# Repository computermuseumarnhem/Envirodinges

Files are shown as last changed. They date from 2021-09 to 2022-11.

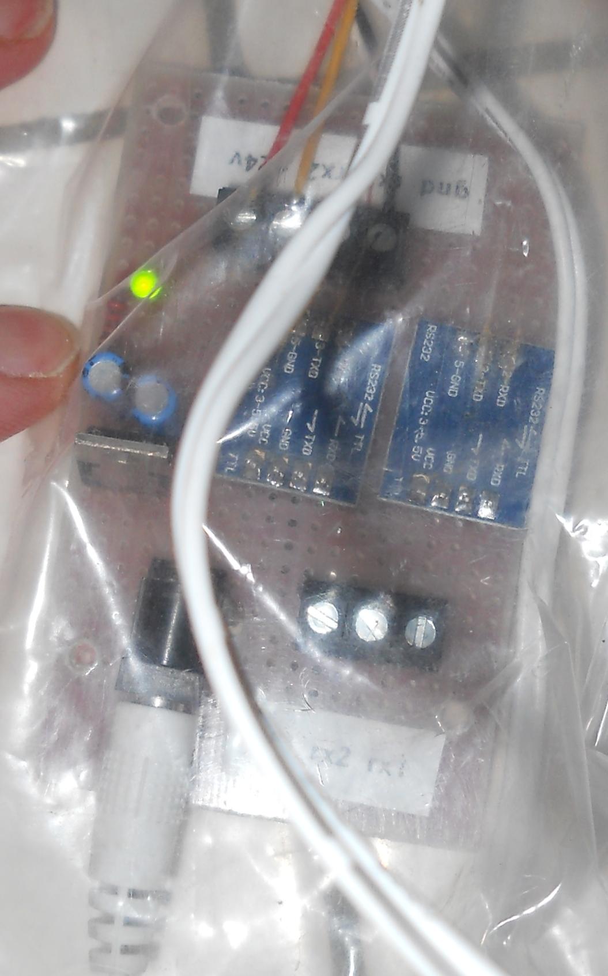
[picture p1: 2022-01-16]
dscn2125_crop.jpg

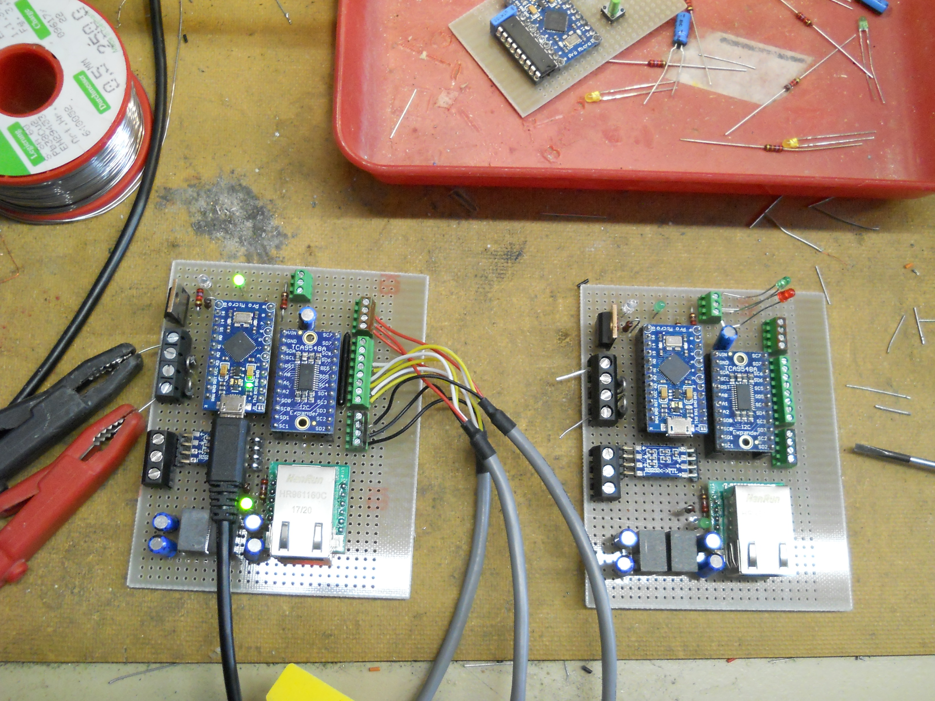
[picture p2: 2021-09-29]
dscn2068.jpg

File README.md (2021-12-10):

# Envirodinges
Veredelde fan controller voor het ventileren van de opslagcontainers. 

Fan aan/uit wordt gestuurd door een Arduino Pro Micro op basis van AM2315 thermo/hygro sensors (1 buiten, 2 binnen) zodat er geventileerd wordt als de luchttemperatuur >10C boven de dauwpunttemperatuur ligt waardoor er binnen geen kans is op condens van de aangezogen lucht.

Status output 1x/minuut via RS232, zie Envirodinges.log.

LAN hardware met W5500 TCP/IP chip aanwezig, maar niet gebruikt door gebrek aan programmaruimte.

Omdat de AM2315 geen instelbaar I2C adres heeft worden ze via een multiplexer (TCA9548) aangesloten.

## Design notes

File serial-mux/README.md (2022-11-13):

# Serial Multiplexer.

## Envirodinges

De twee Envirodingesen sturen regels over twee RS232-lijnen naar iets wat ze zou kunnen loggen.

## Multiplexer

Een Pro Micro met een hardware serial en een software serial leest
deze RS232 lijnen en (omdat de containers zelf de prefix met 'container1' of 'container2' doet) buffert
ze per regel en stuurt ze door via de USB-serial.

De Pro Micro is gemonteerd op een board met schroefaansluitingen, die is eigenlijk bedoeld voor de Arduino Nano, maar
de Pro Micro past ook.

### Seriele poorten

Omdat de SoftwareSerial op de Pro Micro (ATmega32U4) alleen werkt op poorten waar een pin change interrupt actief kan zijn, worden pin 8 en 9 voor respectievelijk RX en TX gebruikt. De vorige versies op respectievelijk pin 4 en 5, daarna 2 en 3 bleken niet te werken totdat ik de handleiding beter had gelezen.

## Wat te doen met de data

Een IOTStack-gebaseerde Pi (Mosquitto, NodeRed, InfluxDB, Grafana) is ingericht om alles te kunnen netwerken.

- NodeRed luistert naar de USB-serial, vertaalt de puntjes naar slashes en publiceert de key/value pairs als topic/payload naar de Mosquitto MQTT broker.
- NoderRed stuurt de key/value pairs ook naar InfluxDB
- Grafana leest InfluxDB en maakt er shiny plaatjes van.

Bovenstaande kan natuurlijk allemaal gescrapt worden als gebruik kan worden gemaakt van een al bestaande machine die USB-serial kan lezen, en de gegevens naar een reeds bestaande MQTT te sturen. Et Cetera.

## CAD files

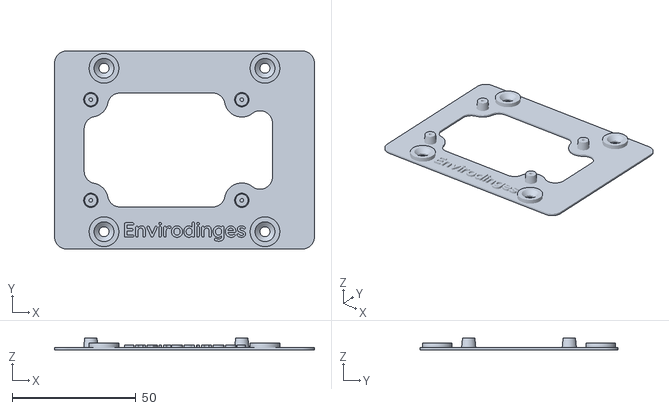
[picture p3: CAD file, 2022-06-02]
serial-mux/bevestiging/serial-module.stl
105.0 x 80.0 x 5.00

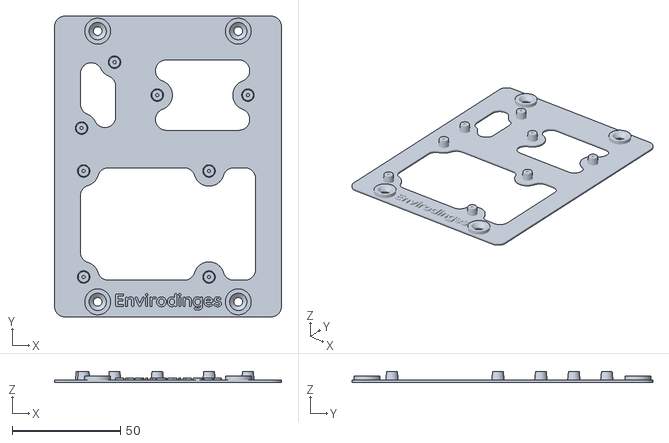
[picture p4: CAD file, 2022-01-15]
serial-mux/bevestiging/bevestiging.stl
105.0 x 139.2 x 5.00

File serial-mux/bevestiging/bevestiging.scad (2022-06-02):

$fn = 90;

want="serial";

function inch(n) = 25.4 * n;

PI_BOARD = [85, 56, 1.25];
PWR_BOARD = [inch(0.80), inch(1.70), inch(0.04)];
NANO_BOARD = [53, 36.5, inch(0.05)];
SERIAL_BOARD = [80, 50, 1.6];

PI_HOLE_LOCATIONS =	[[3.5, 3.5], [61.5, 3.5], [3.5, 52.5], [61.5, 52.5]];
PWR_HOLE_LOCATIONS = [[inch(0.10), inch(0.25)], [inch(0.70), inch(1.45)]];
NANO_HOLE_LOCATIONS = [[26.5-inch(1.65/2), 36.5/2], [26.5+inch(1.65/2), 36.5/2]];

SERIAL_MARGIN = SERIAL_BOARD.y/2 - inch(1.6/2);

SERIAL_HOLE_LOCATIONS = [
    [SERIAL_MARGIN, SERIAL_MARGIN],
    [SERIAL_MARGIN + inch(2.4), SERIAL_MARGIN],
    [SERIAL_MARGIN, SERIAL_MARGIN + inch(1.6)],
    [SERIAL_MARGIN + inch(2.4), SERIAL_MARGIN + inch(1.6)]
];

echo(SERIAL_HOLE_LOCATIONS);
module chamfer(radius) {
    offset(r=radius) offset(r=-radius) children();
}

module plaat(size, radius, flat=false) {
    if (flat) {
        chamfer(radius) square([size.x, size.y]);
    } else {
        linear_extrude(size.z) plaat(size, radius, true);
    }
}

module center(dim) {
    //translate(-[dim.x, dim.y, 0]/2) 
        children();
}

module pi_board(h = 0, flat=false) {
    translate([0, 0, h]) center(PI_BOARD) plaat(PI_BOARD, 3.5, flat);
}
module pwr_board(h = 0, flat=false) {
    translate([0, 0, h]) center(PWR_BOARD) plaat(PWR_BOARD, 0, flat);
}
module nano_board(h = 0, flat=false) {
    translate([0, 0, h]) center(NANO_BOARD) plaat(NANO_BOARD, 0, flat);
}

module serial_board(h = 0, flat=false) {
    translate([0, 0, h]) center(SERIAL_BOARD) plaat(SERIAL_BOARD, 0, flat);
}

module pi_hole_locations() {
    center(PI_BOARD) {
        for (hole = PI_HOLE_LOCATIONS) {
            translate(hole) children();
        }
    }
}
module pwr_hole_locations() {
    center(PWR_BOARD) {
        for (hole = PWR_HOLE_LOCATIONS) {
            translate(hole) children();
        }
    }
}
module nano_hole_locations() {
    center(NANO_BOARD) {
        for (hole = NANO_HOLE_LOCATIONS) {
            translate(hole) children();
        }
    }
}

module serial_hole_locations() {
    center(SERIAL_BOARD) {
        for (hole = SERIAL_HOLE_LOCATIONS) {
            translate(hole) children();
        }
    }
}  

module post() {
    difference() {
        cylinder(d1=6, d2=5, h=5);
        cylinder(d=1.5, h=5);
    }
}

module mount(diff=false) {
    if (!diff) {
        cylinder(d=12, h=3);
    } else {
        cylinder(d=4, h=3);
        translate([0,0,1]) cylinder(d1=4, d2=8, h=2);
    }
}

module mqtt_holes(mounts) {
    
    linear_extrude(2)
    chamfer(5) offset(r=-2)
    difference() {
        union() {
            translate([ pi_top, pi_left, 0]) {
                pi_board(flat=true);
            }
            translate([ pwr_top,  pwr_left, 0]) {
                pwr_board(flat=true);
            }
            translate([ nano_top,  nano_left, 0]) {
                nano_board(flat=true);
            }
        };
        for (m = mounts) {
            translate(m) circle(d=14);
        }
        translate([ pi_top, pi_left, 0]) {
            pi_hole_locations() circle(d=10);
        }
        translate([ pwr_top,  pwr_left, 0]) {
            pwr_hole_locations() circle(d=10);
        }
        translate([ nano_top,  nano_left, 0]) {
            nano_hole_locations() circle(d=10);
        }
    }
}


module serial_holes(mounts) {
    
    linear_extrude(2)
    chamfer(5) offset(r=-2)
    difference() {
        union() {
            translate([ serial_top, serial_left, 0]) {
                serial_board(flat=true);
            }
        };
        for (m = mounts) {
            translate(m) circle(d=14);
        }
        translate([ serial_top, serial_left, 0]) {
            serial_hole_locations() circle(d=10);
        }
    }
}


module name(t) {
    linear_extrude(2)
        text(t, font="Quicksand:style=Bold", size=6, halign="center", valign="center");
}

pi_left = 0;
pwr_left = pi_left + PI_BOARD.y + 10;
nano_left = pwr_left + PWR_BOARD.y/2 - (NANO_BOARD.y/2);

serial_left = 0;

pi_top = 0;
pwr_top = 0;
nano_top = pi_top + PI_BOARD.x - NANO_BOARD.x;

serial_top = 0;

module mqtt_module() {

    base_left = -15;
    base_top = -10;
    base_width = 15 + PI_BOARD.y + 10 + PWR_BOARD.y + 15;
    base_height = 10 + PI_BOARD.x + 10;


    translate([ pi_top, pi_left, 0]) {
        % pi_board(5);
        pi_hole_locations() post();
    }
    translate([ pwr_top,  pwr_left, 0]) {
        % pwr_board(5);
        pwr_hole_locations() post();
    }
    translate([ nano_top,  nano_left, 0]) {
        % nano_board(5);
        nano_hole_locations() post();
    }

    from_top = 20;
    from_left = 7;
    mounts = [
        [ base_top + from_top,                base_left + from_left              ],
        [ base_top + from_top,                base_left + base_width - from_left ],
        [ base_top + base_height - from_top,  base_left + from_left              ],
        [ base_top + base_height - from_top,  base_left + base_width - from_left ]
    ];

    difference() {
        union() {
            translate([base_top, base_left, 0]) {
                plaat([base_height, base_width, 1], 5);
            }
            for (m = mounts) {
                translate(m) mount();
            }
        };
        for (m = mounts) {
            translate(m) mount(true);
        }
        mqtt_holes(mounts);
    }

    text_center = [(mounts[0].x + mounts[2].x)/2, mounts[0].y];

    translate(text_center) name("Envirodinges");

}
module serial_module() {

    base_left = -15;
    base_top = -10;
    base_width = 15 + SERIAL_BOARD.y + 15;
    base_height = 10 + PI_BOARD.x + 10;


    translate([ serial_top, serial_left, 0]) {
        % serial_board(5);
        serial_hole_locations() post();
    }
    
    from_top = 20;
    from_left = 7;
    mounts = [
        [ base_top + from_top,                base_left + from_left              ],
        [ base_top + from_top,                base_left + base_width - from_left ],
        [ base_top + base_height - from_top,  base_left + from_left              ],
        [ base_top + base_height - from_top,  base_left + base_width - from_left ]
    ];

    difference() {
        union() {
            translate([base_top, base_left, 0]) {
                plaat([base_height, base_width, 1], 5);
            }
            for (m = mounts) {
                translate(m) mount();
            }
        };
        for (m = mounts) {
            translate(m) mount(true);
        }
        serial_holes(mounts);
    }

    text_center = [(mounts[0].x + mounts[2].x)/2, mounts[0].y];

    translate(text_center) name("Envirodinges");

}


if (want=="mqtt") {
    mqtt_module();
}
if (want=="serial") {
    serial_module();
}

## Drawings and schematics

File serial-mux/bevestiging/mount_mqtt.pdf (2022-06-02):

# /home/denz/Drive/CMA/Envirodinges/serial-mux/bevestiging/bevestiging.scad

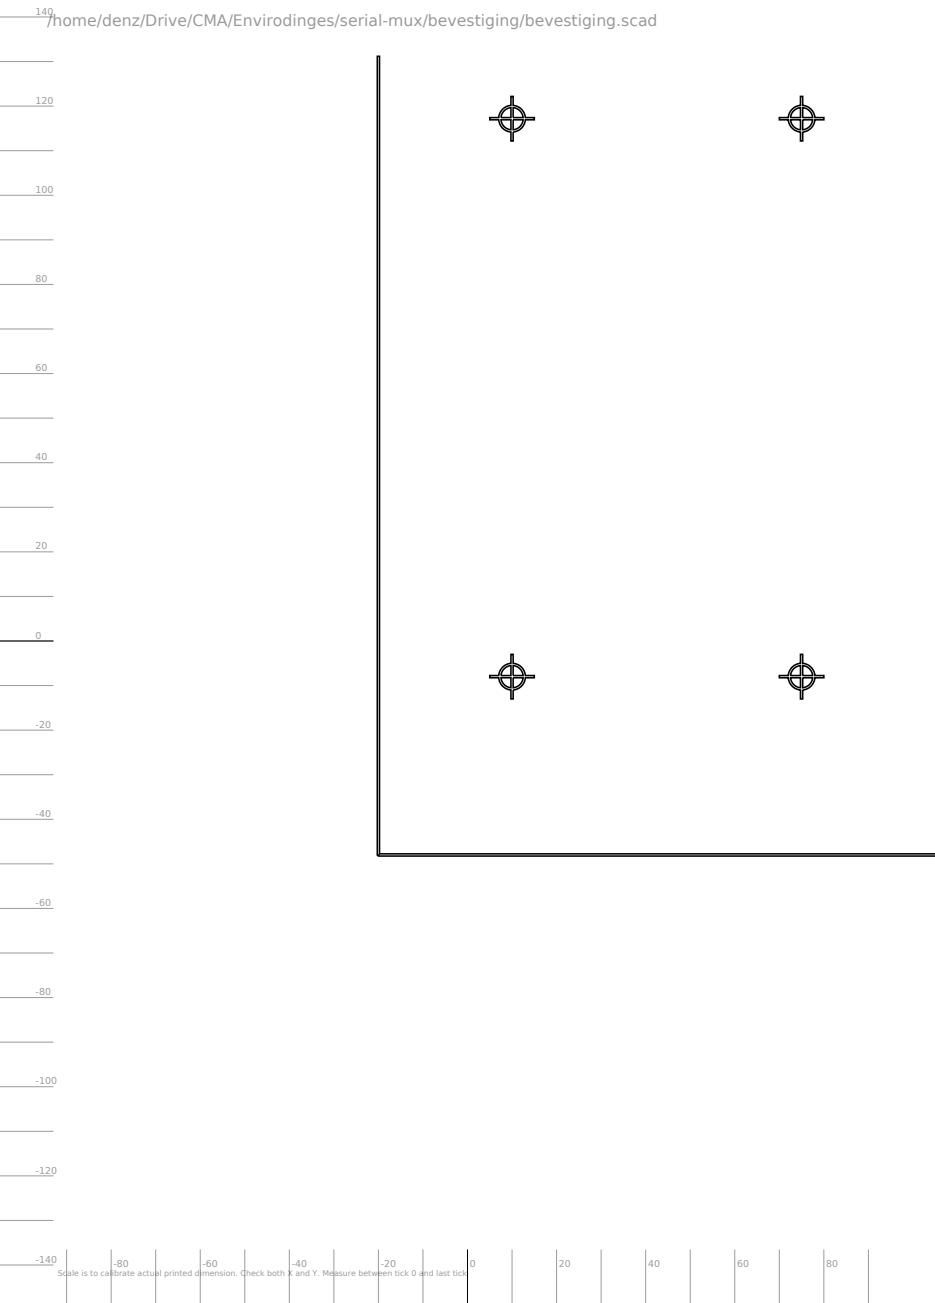
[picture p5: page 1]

Scale is to calibrate actual printed dimension. Check both X and Y. Measure between tick 0 and last tick

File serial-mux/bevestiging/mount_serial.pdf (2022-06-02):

# /home/denz/Drive/CMA/Envirodinges/serial-mux/bevestiging/bevestiging.scad

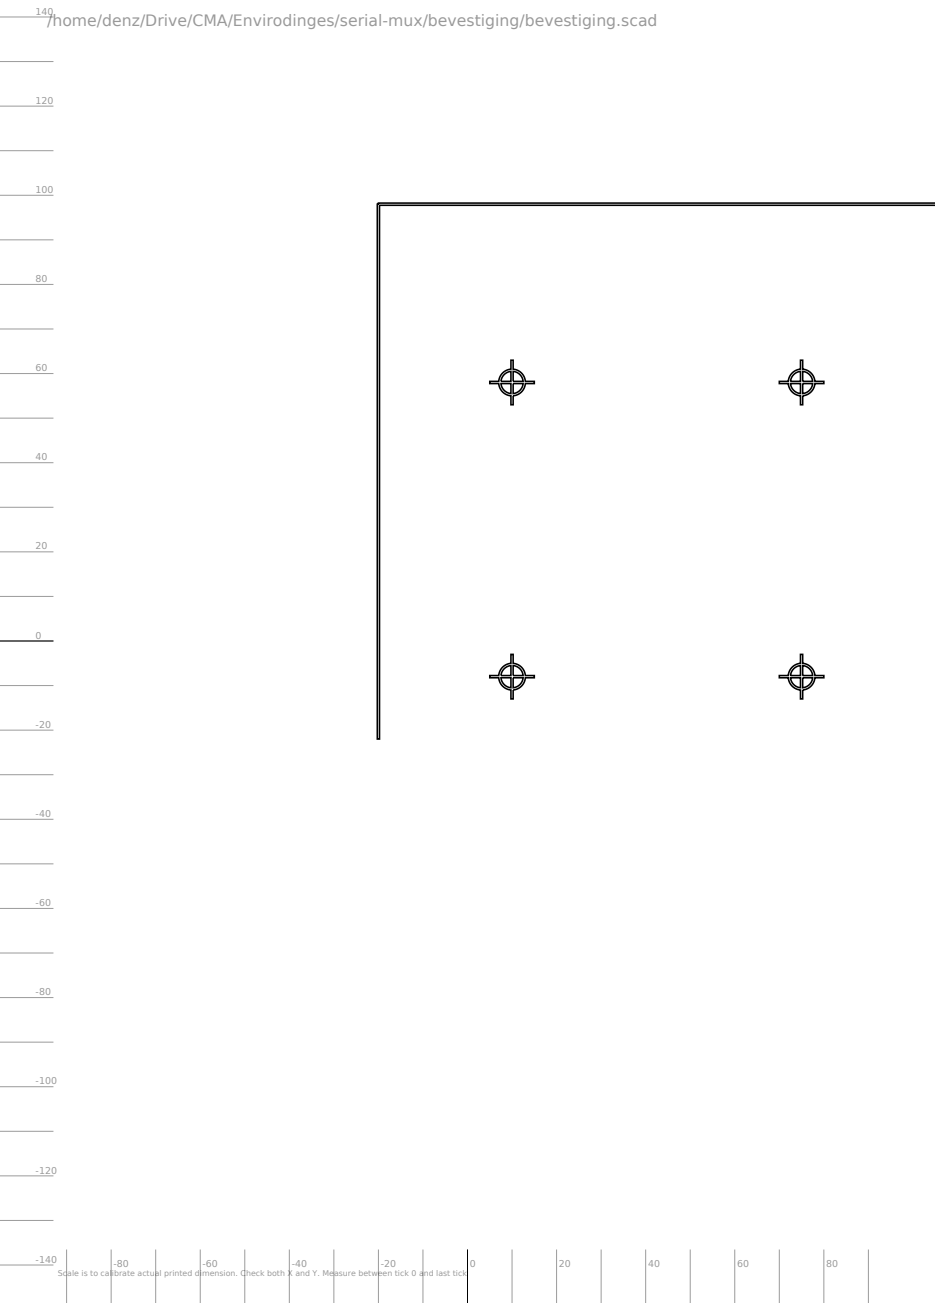
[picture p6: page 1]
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

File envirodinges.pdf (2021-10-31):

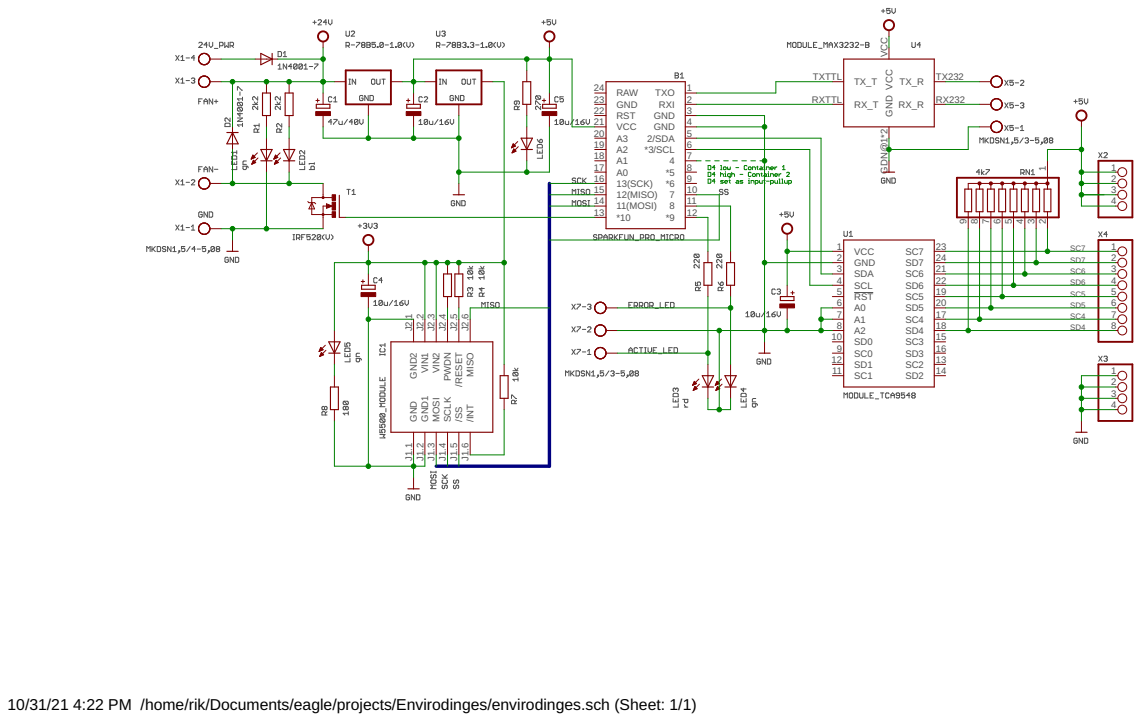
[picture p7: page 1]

7 8 9 10

10/31/21 4:22 PM /home/rik/Documents/eagle/projects/Envirodinges/envirodinges.sch (Sheet: 1/1)

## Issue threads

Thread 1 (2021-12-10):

Parsing of the serial port output

vandenzel, 2021-12-10:
I'm trying to implement a way to read the output of the Envirodingeses with a machine. So I propose the following changes:

Replace all output lines with a key-value pair like this:

    envirodinges.c1.version 0.9
    envirodinges.c1.s1.status ok
    envirodinges.c1.started
    envirodinges.c1.s1.temp 5.3 C
    envirodinges.c1.s1.hum 94.4 %
    envirodinges.c2.s1.status notfound
    envirodinges.c2.s1.status missing

This way a can just split the values and use value[0] as mqtt (and influxdb) topic, and value[1] as the payload.

--
Alex.

Stoneshop, 2021-12-11:
Will look into this.

vandenzel, 2021-12-13:
Ik zat een beetje hieraan te denken:

De tag is een MQTT topic, en bestaat uit

 * ```envirodinges```
 * de naam van de container (van de envirodinges module)
 * de naam van de sensor (indien van toepassing), bijvoorbeeld ```container1```
 * de grootheid (```temperatuur```, ```status```, etc...)

De waarde is dan in het relevante datatype van de grootheid, en bevat geen spaties. Als er na de waarde een spatie en nog meer tekst staat is dat voor de human-readability en wordt door de machine genegeerd.

Bijvoorbeeld:

    envirodinges/container1/status: ok
    envirodinges/container1/external/status: notfound (check wiring & pullups)
    envirodinges/container1/external/temperature: 15 °C

Of met puntjes (```.```) in plaats van slashes (```/```):

    envirodinges.container1.status: ok
    envirodinges.container1.external.status: notfound (check wiring & pullups)
    envirodinges.container1.external.temperature: 15 °C

Het ```envirodinges``` deel zou weggelaten kunnen worden, dat kan ergens in de serieel-naar-mqtt vertaalslag toegevoegd kunnen worden.

vandenzel, 2022-01-07:
Het werkt nu min of meer. `status.fan.status on` heeft nog geen dubbele punt, maar dat is niet zo spannend meer. ik kan splitsen op spatie en de dubbele punt wegnegeren.

Stoneshop, 2022-01-07:
Dubbele punt staat tussen de meetgrootheid en de meetwaarde, statusmeldingen hebben alleen een spatie als separator

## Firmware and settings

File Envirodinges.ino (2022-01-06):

#define CODEVERSION "0.95"

#undef ETHERNET           // do not define when insufficient memory

#define MOSFET            10
#define ACTIVE_LED        9
#define ERROR_LED         8
#define CONTAINER_SELECT  5

#include <PrintEx.h>
#include <Wire.h>
#include <Adafruit_AM2315.h>
#include <math.h>

#ifdef ETHERNET
#include <SPI.h>
#include <Ethernet.h>
#include <Adafruit_MQTT.h>
#endif

PrintEx PSerial = Serial;
PrintEx PSerial1 = Serial1;

#define I2C_ROMADDRESS  0x53
#define I2C_TCAADDR     0x70
#define W5500_CS        7

static uint8_t mac[] = { 0x90, 0xA2, 0xDA, 0x42, 0x42, 0x00 };
static char outline[80];

byte containernum;
bool b_sensor_present[4], b_network;
bool b_errled = false;
byte brightness = 128;    // how bright the LED is
byte fadeAmount = 8;    // how many points to fade the LED by
long nextrun = 0;
long nextfade = 0;
long nextfanshow = 0;
long nexterrorled = 0;
long errorledinterval = 65000; // > 1 minute
char * sensorname[4] = { "external", "inlet", "outlet", "spare" };

#define RUNINTERVAL   60000	// 1 minute
#define FADEINTERVAL  64

#define TDEW_DIFF     10.0  // fan off if dewpoint too close to temperature
#define HUMID_MIN     45.0  // fan on if humidity inside exceeded

// #define SENSORCOUNT_4  // only if 4 AM2315 sensors
#define MUX_OFFSET  3
#define I2CMUX_L    4

Adafruit_AM2315 am2315_1;
Adafruit_AM2315 am2315_2;
Adafruit_AM2315 am2315_3;
#ifdef SENSORCOUNT_4
  const byte sensor_required = 4;  
  Adafruit_AM2315 am2315_4;
  #define I2CMUX_H    7
#else
  const byte sensor_required = 3; 
  #define I2CMUX_H    6 
#endif


void set_i2c_mux(byte i2c_sel) {
  if ((i2c_sel < I2CMUX_L) || (i2c_sel > I2CMUX_H)) return;
 
  Wire.beginTransmission(I2C_TCAADDR);
  Wire.write(1 << i2c_sel);
  Wire.endTransmission();  
  delay(250);
}

void fanswitch(bool state)
{
  digitalWrite(MOSFET, state);
  nextfanshow = millis() + 5000;
}

void outputvalue(uint8_t sensor, char * outstr)
{
  char buf[80];

//  Serial.print(strlen(outstr));
//  Serial.print("  ");
  memset(buf, 0, 80);
  sprintf(buf, "container%d.sensor.%s.%s", containernum, sensorname[sensor-1], outstr);
  if (Serial) Serial.println(buf);
  Serial1.println(buf);
  memset(outstr, 0, 80);
}

void outputstatus(char * outstr)
{
  char buf[80];

//  Serial.print(strlen(outstr));
//  Serial.print("  ");
  memset(buf, 0, 80);
  sprintf(buf, "container%d.status.%s", containernum, outstr);
  if (Serial) Serial.println(buf);
  Serial1.println(buf);
  memset(outstr, 0, 80);
}
#ifdef ETHERNET
void printIPAddress()
{
  IPAddress myIp = Ethernet.localIP();
  sprintf(outline, "IP: %d.%d.%d.%d\0", myIp[0], myIp[1], myIp[2], myIp[3]);
}
#endif

void setup() {
  byte sensor_index;
  b_network = false;

  Serial.begin(9600);
  Serial1.begin(9600);
  delay(5000);

  
  pinMode(MOSFET, OUTPUT);
  pinMode(ACTIVE_LED, OUTPUT);
  pinMode(ERROR_LED, OUTPUT);
  analogWrite(ACTIVE_LED, 128);
  digitalWrite(ERROR_LED, true);
  digitalWrite(MOSFET, true);

  pinMode(CONTAINER_SELECT, INPUT_PULLUP);
  if (digitalRead(CONTAINER_SELECT) == LOW) {
     mac[5] = 0x01;  
     containernum = 1;
  }
  else
  {
     mac[5] = 0x02;  
     containernum = 2;
  }
  sprintf(outline, "init.version %s\0", CODEVERSION); 
  outputstatus(outline);
  sprintf(outline, "init.container %d\0", containernum); 
  outputstatus(outline);

#ifdef ETHERNET
  Ethernet.init(W5500_CS); 
#endif   
  Wire.begin();  
  for (sensor_index=1; sensor_index<=sensor_required; sensor_index++) {
    b_sensor_present[sensor_index] = false;
    set_i2c_mux(sensor_index + MUX_OFFSET);
    delay(500);
    switch (sensor_index) {
      case 1:
        b_sensor_present[sensor_index] = am2315_1.begin();
        break;
      case 2:
        b_sensor_present[sensor_index] = am2315_2.begin();
        break;
      case 3:
        b_sensor_present[sensor_index] = am2315_3.begin();
        break;
#ifdef SENSORCOUNT_4          
      case 4:
        b_sensor_present[sensor_index] = am2315_4.begin();
        break;
#endif          
    }
    // memset(outline, 0, 80);
    if (b_sensor_present[sensor_index]) {
      sprintf(outline, "%s\0", "status OK\0");
    }
    else {
      sprintf(outline, "%s\0", "status missing - check wiring & pullups!"); 
    }
    outputvalue(sensor_index, outline);
    delay(1000);     
  }
  // memset(outline, 0, 80);
  sprintf(outline, "%s\0", "code starting");
  outputstatus(outline);
  
#ifdef ETHERNET  
  // memset(outline, 0, 80);
  sprintf(outline, "MAC: %02x:%02x:%02x:%02x:%02x:%02x\n\0", mac[0], mac[1], mac[2], mac[3], mac[4], mac[5]);
  output(statusoutline);
  // start Ethernet and UDP
  auto link = Ethernet.linkStatus();
  // memset(outline, 0, 80);
  switch (link) {
    case Unknown:
      sprintf(outline, "netw0rk.linkstatus %s\0", "Unknown");
      break;
    case LinkON:
      sprintf(outline, "network.linkstatus %s\0", "UP");
      b_network = true;
      break;
    case LinkOFF:
      sprintf(outline, "network.linkstatus %s\0", "DOWN");
      b_network = true;
      break;
  }
  outputstatus(outline);

  if (b_network) {
    if (Ethernet.begin(mac) == 0) {
      b_network = false;
      // memset(outline, 0, 80);
      sprintf(outline, "%s\0", "network.dhcp fail");
      outputstatus(outline);
    }
    else {
      printIPAddress();
      b_network = true;
      digitalWrite(ERROR_LED, false);
    }
  }
#endif
  digitalWrite(ERROR_LED, false);
  nexterrorled = millis();
  fanswitch(false);
}

float dewpoint(float t, float h) {
  //  A = Log(RH / 100) / Log(2.718282) + (17.62 * Ta / (243.12 + Ta))
  //  Td = 243.12 * A / (17.62 - A) grdC
  
  float tdew, a;

  a = log(h/100) / (log(2.718282) + (17.62 * t / (243.12 + t)));
  tdew = 243.12 * a / (17.62 - a);
  return tdew;
}

void loop() {
  // put your main code here, to run repeatedly:

  byte sensor_index;
  float temps[4], humids[4], tdew[4];
  float tint_min, tint_max, humidint_max, tdew_max, tdew_fan;
  bool b_fanon, b_readok, b_sensorfault;

  char *fanstate[] { "off", "on" };


  if (millis() > nextrun) {
    nextrun += RUNINTERVAL;
    b_sensorfault = false;

    for (sensor_index=1; sensor_index<=sensor_required; sensor_index++) {
        set_i2c_mux((sensor_index + MUX_OFFSET));
        delay(500);
        switch (sensor_index) {
          case 1:   // external sensor
            b_readok = am2315_1.readTemperatureAndHumidity(&temps[1], &humids[1]);
            break;
          case 2:   // internal sensor, inlet
            b_readok = am2315_2.readTemperatureAndHumidity(&temps[2], &humids[2]);
            break;
          case 3:   // internal sensor, outlet
            b_readok = am2315_3.readTemperatureAndHumidity(&temps[3], &humids[3]);
            break;
#ifdef SENSORCOUNT_4           
          case 4:
            b_readok = am2315_4.readTemperatureAndHumidity(&temps[4], &humids[4]);
            break;
#endif
        };
        // memset(outline, 0, 80);
        if (b_readok == false) {
          b_sensorfault = true;
          sprintf(outline, "%s\0", "status missing\0");
        }
        else {
          tdew[sensor_index] = dewpoint(temps[sensor_index], humids[sensor_index]);
          sprintf(outline, "temp: %2.1fC\0", temps[sensor_index]);
          outputvalue(sensor_index, outline); 
          sprintf(outline, "hum:  %2.1f%%\0", humids[sensor_index]);
          outputvalue(sensor_index, outline); 
          sprintf(outline, "dewpt: %2.1fC\0", tdew[sensor_index])
        }
        outputvalue(sensor_index, outline); 
    }
    // memset(outline, 0, 80);
    if (b_sensorfault == false) { 
      tint_max = max(temps[2], temps[3]);           // highest temp inside
      tint_min = min(temps[2], temps[3]);           // lowest temp inside
      humidint_max = max(humids[2], humids[3]);     // highest humidity inside
      tdew_max = dewpoint(tint_min, humidint_max);  // highest dewpoint inside
      tdew_fan = dewpoint(tint_min, humids[1]);     // inside temp against outside humidity
      b_fanon = (humidint_max > HUMID_MIN);         // fan on if humid inside
      b_fanon = b_fanon && ((tint_min - TDEW_DIFF) > tdew_fan) ; // ... unless chance of condensation
      sprintf(outline, "fan.min.temp.intern: %2.1fC\0", tint_min);
      outputstatus(outline);
      sprintf(outline, "fan.humid.extern: %2.1f%%\0", humids[1]);
      outputstatus(outline);
      sprintf(outline, "fan.dewpt: %2.1fC\0", tdew_fan);
      outputstatus(outline);
      sprintf(outline, "fan.status %s\0", fanstate[b_fanon]);
    }
    else {
      b_fanon = false;
      sprintf(outline, "fan.status %s\0", "off - sensor read error");
    }
    outputstatus(outline);
    fanswitch(b_fanon);
#ifdef ETHERNET
    if (!b_network) {
      errorledinterval = 10000;
    }
#endif
    
    if (b_sensorfault) { 
      errorledinterval = 2000; 
    }
    else {
      errorledinterval = 65000;
    }
  }

  if (millis() > nextfanshow) {   // show controller activity
    if (millis() > nextfade) {              
      nextfade += FADEINTERVAL;     // wait for FADEINTERVAL milliseconds to see the dimming effect
      analogWrite(ACTIVE_LED, brightness);

      // change the brightness for next time through the loop:
      brightness = brightness + fadeAmount;
      // reverse the direction of the fading at the ends of the fade:
      if (brightness < 8 || brightness >= 248) {
        fadeAmount = -fadeAmount;
      }    
    }
  }
  else {                        // show fan state for 5 seconds
    if (b_fanon == true) {
      brightness = 240;   
    }
    else
    {
      brightness = 8;
    }
    analogWrite(ACTIVE_LED, brightness);
  }

  if (millis() > nexterrorled) {
    nexterrorled += errorledinterval;
    if (errorledinterval < 60000) { // error condition
      if (b_errled != false ) {
        b_errled = false;
      }
      else {
        b_errled = true;    
      }
    }
    else {
      b_errled = false;
    }
    digitalWrite(ERROR_LED, b_errled);
  }
}

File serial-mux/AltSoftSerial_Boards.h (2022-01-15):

/* An Alternative Software Serial Library
 * http://www.pjrc.com/teensy/td_libs_AltSoftSerial.html
 * Copyright (c) 2014 PJRC.COM, LLC, Paul Stoffregen, paul@pjrc.com
 * 
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
 * THE SOFTWARE IS PROVIDED "AS IS", WITHOUT WARRANTY OF ANY KIND, EXPRESS OR
 * IMPLIED, INCLUDING BUT NOT LIMITED TO THE WARRANTIES OF MERCHANTABILITY,
 * FITNESS FOR A PARTICULAR PURPOSE AND NONINFRINGEMENT. IN NO EVENT SHALL THE
 * AUTHORS OR COPYRIGHT HOLDERS BE LIABLE FOR ANY CLAIM, DAMAGES OR OTHER
 * LIABILITY, WHETHER IN AN ACTION OF CONTRACT, TORT OR OTHERWISE, ARISING FROM,
 * OUT OF OR IN CONNECTION WITH THE SOFTWARE OR THE USE OR OTHER DEALINGS IN
 * THE SOFTWARE.
 */


// Teensy 2.0
//
#if defined(__AVR_ATmega32U4__) && defined(CORE_TEENSY)

 //#define ALTSS_USE_TIMER1
 //#define INPUT_CAPTURE_PIN		22 // receive
 //#define OUTPUT_COMPARE_A_PIN		14 // transmit
 //#define OUTPUT_COMPARE_B_PIN		15 // unusable PWM
 //#define OUTPUT_COMPARE_C_PIN		 4 // unusable PWM

 #define ALTSS_USE_TIMER3
 #define INPUT_CAPTURE_PIN		10 // receive
 #define OUTPUT_COMPARE_A_PIN		 9 // transmit



// Teensy++ 2.0
//
#elif defined(__AVR_AT90USB1286__) && defined(CORE_TEENSY)

 #define ALTSS_USE_TIMER1
 #define INPUT_CAPTURE_PIN		 4 // receive
 #define OUTPUT_COMPARE_A_PIN		25 // transmit
 #define OUTPUT_COMPARE_B_PIN		26 // unusable PWM
 #define OUTPUT_COMPARE_C_PIN		27 // unusable PWM

 //#define ALTSS_USE_TIMER3
 //#define INPUT_CAPTURE_PIN		17 // receive
 //#define OUTPUT_COMPARE_A_PIN		16 // transmit
 //#define OUTPUT_COMPARE_B_PIN		15 // unusable PWM
 //#define OUTPUT_COMPARE_C_PIN		14 // unusable PWM


// Teensy 3.x
//
#elif defined(__MK20DX128__) || defined(__MK20DX256__) || defined(__MK64FX512__) || defined(__MK66FX1M0__)
 #define ALTSS_USE_FTM0
 #define INPUT_CAPTURE_PIN		20 // receive       (FTM0_CH5)
 #define OUTPUT_COMPARE_A_PIN		21 // transmit      (FTM0_CH6)
 #define OUTPUT_COMPARE_B_PIN		22 // unusable PWM  (FTM0_CH0)
 #define OUTPUT_COMPARE_C_PIN		23 // PWM usable fixed freq
 #define OUTPUT_COMPARE_D_PIN		 5 // PWM usable fixed freq
 #define OUTPUT_COMPARE_E_PIN		 6 // PWM usable fixed freq
 #define OUTPUT_COMPARE_F_PIN		 9 // PWM usable fixed freq
 #define OUTPUT_COMPARE_G_PIN		10 // PWM usable fixed freq


// Wiring-S
//
#elif defined(__AVR_ATmega644P__) && defined(WIRING)

 #define ALTSS_USE_TIMER1
 #define INPUT_CAPTURE_PIN		 6 // receive
 #define OUTPUT_COMPARE_A_PIN		 5 // transmit
 #define OUTPUT_COMPARE_B_PIN		 4 // unusable PWM



// Arduino Uno, Duemilanove, LilyPad, etc
//
#elif defined(__AVR_ATmega168__) || defined(__AVR_ATmega328P__)

 #define ALTSS_USE_TIMER1
 #define INPUT_CAPTURE_PIN		 8 // receive
 #define OUTPUT_COMPARE_A_PIN		 9 // transmit
 #define OUTPUT_COMPARE_B_PIN		10 // unusable PWM


// Arduino Leonardo & Yun (from Cristian Maglie)
//
#elif defined(ARDUINO_AVR_YUN) || defined(ARDUINO_AVR_LEONARDO) || defined(__AVR_ATmega32U4__)

  #define ALTSS_USE_TIMER1
  #define INPUT_CAPTURE_PIN		4  // receive
  #define OUTPUT_COMPARE_A_PIN	9 // transmit
  #define OUTPUT_COMPARE_B_PIN	10 // unusable PWM
  #define OUTPUT_COMPARE_C_PIN	11 // unusable PWM

  //#define ALTSS_USE_TIMER3
  //#define INPUT_CAPTURE_PIN		13 // receive
  //#define OUTPUT_COMPARE_A_PIN		5 // transmit


// Arduino Mega
//
#elif defined(__AVR_ATmega1280__) || defined(__AVR_ATmega2560__)

 //#define ALTSS_USE_TIMER4
 //#define INPUT_CAPTURE_PIN		49 // receive
 //#define OUTPUT_COMPARE_A_PIN		 6 // transmit
 //#define OUTPUT_COMPARE_B_PIN		 7 // unusable PWM
 //#define OUTPUT_COMPARE_C_PIN		 8 // unusable PWM

 #define ALTSS_USE_TIMER5
 #define INPUT_CAPTURE_PIN		48 // receive
 #define OUTPUT_COMPARE_A_PIN		46 // transmit
 #define OUTPUT_COMPARE_B_PIN		45 // unusable PWM
 #define OUTPUT_COMPARE_C_PIN		44 // unusable PWM



// Sanguino
#elif defined(__AVR_ATmega644P__) || defined(__AVR_ATmega644__)
 #define ALTSS_USE_TIMER1
 #define INPUT_CAPTURE_PIN		14 // receive
 #define OUTPUT_COMPARE_A_PIN		13 // transmit
 #define OUTPUT_COMPARE_B_PIN		12 // unusable PWM


// Unknown board
#else
#error "Please define your board timer and pins"
#endif

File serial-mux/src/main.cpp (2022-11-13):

/*
 * Serial multiplexer.
 *
 * Two real serial ports can receive lines of text and
 * transmit these over the virtual serial port (USB) of
 * a Arduino Pro Micro
 *
 * Connections:
 *
 * Serial: Virtual serial port over USB (/dev/ttyUSBx on the Pi)
 * Serial1: HardwareSerial port of the Pro Micro
 *    - RXI (pin 0)
 *    - TXO (pin 1), unused
 * Serial2: SoftwareSerial
 *    - RXI (pin 8)
 *    - TXO (pin 9), unused
 *
 *      -------------
 *  10  |             |  9  TX   Serial2
 *  16  |             |  8  RX   Serial2
 *  14  |             |  7
 *  15  |             |  6
 *  18  |             |  5
 *  19  |             |  4
 *  20  |             |  3
 *  21  |             |  2
 * VCC  |             | GND
 * RST  |             | GND
 * GND  |    -----    |  0  RX   Serial1
 * RAW  |   |     |   |  1  TX   Serial1
 *       ---|     |---
 *           -----
 *                       USB
 *
 */

#define SERIAL1_RX 0
#define SERIAL1_TX 1
#define SERIAL2_RX 8
#define SERIAL2_TX 9

#include <Arduino.h>
#include <SoftwareSerial.h>

SoftwareSerial Serial2(SERIAL2_RX, SERIAL2_TX);
String Buffer1;
String Buffer2;

class Timer {
private:
    bool _rollover;
    unsigned long _timeout;
    unsigned long _next;

public:
    Timer(unsigned long timeout) {
        _timeout = timeout;
        next();
    }

    bool next() {
        unsigned long now = millis();

        if (_rollover) {
            if (now < _next) {  // millis() has also rolled over
                _rollover = false;
            }
            return false;  // still not ready for action
        }

        if (now > _next) {  // ready for action
            _next = now + _timeout;
            if (_next < now) {  // _next rolled over
                _rollover = true;
            }
            return true;
        }

        return false;
    }
};

Timer timer(10000);

void setup() {
    Serial.begin(115200);
    Serial1.begin(9600);
    Serial2.begin(9600);
    Serial2.listen();
    Buffer1 = "";
    Buffer2 = "";

    // Waiting for the USB Serial to be connected
    // is not necessary nor wanted

    delay(5000);

    Serial.println("envirodinges.status: started");
}

void ProcessChar(String &buffer, const char c) {
    switch (c) {
        case '\r':
            break;  // ignore
        case '\n':
            Serial.println("envirodinges." + buffer);
            buffer = "";
            break;
        default:
            buffer += c;
            break;
    }
}

void loop() {
    if (Serial1.available()) {
        char c = Serial1.read();
        ProcessChar(Buffer1, c);
    }

    if (Serial2.available()) {
        char c = Serial2.read();
        ProcessChar(Buffer2, c);
    }
    if (timer.next()) {
        Serial.println("envirodinges.status: alive");
    }
}

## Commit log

2021-09-29 Version 0.4
    Detecting and reading sensors works, condition for switching the fan to be added, logging to Serial1 (RS232, 9600, 8N1) to be added
2021-09-29 Version 0.4
    Detecting and reading sensors works, condition to switch fan to be determined, logging to Serial1 (RS232, 9600N81) and MQTT to be added
2021-10-25 Add files via upload
    Some more error handling when sensors fail
    TBD: ignore one bad internal sensor, fail if external or both internal bad
    [Envirodinges.ino]
2021-10-27 Add files via upload
    TTL<->RS232 module met echte DB9 connector
    [envirodinges.sch]
2021-10-30 V0.9
    Status fan getoond via activity led
    Error led toont meest relevante error
    Seriele output verbeterd
    Netwerk en MQTT uitgecomment wegens code size
    [Envirodinges.ino]
2021-10-31 V0.91
    Paar ongebruikte variabelen opgeruimd
    Code voor error en activity leds aangepast
    [Envirodinges.ino]
2021-10-31 Ander RS232 module
    [envirodinges.sch]
2021-12-10 V0.92
    Invert container number detection
    Add sensor names
    Some cleanup
    [Envirodinges.ino]
2022-01-15 Serial multiplexer
    [bevestiging.scad, bevestiging.stl]
